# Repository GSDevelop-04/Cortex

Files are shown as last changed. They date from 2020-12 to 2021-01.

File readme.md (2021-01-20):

<br/>
<p align="center">
   <a href="https://github.com/GSDevelop-04/Cortex">
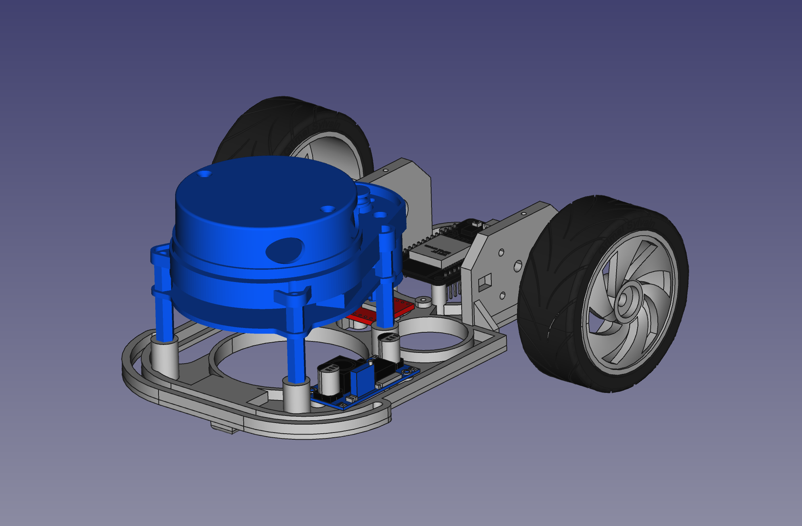
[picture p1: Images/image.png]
    
   </a>
   <br/>
   Plateforme de découverte et d'étude de L'Intelligence Artificielle<br/>
   Véhicule autonome 
</p>

##    1) Introduction

Cortex est un véhicule d'étude de l'Intelligence Artificielle avec réseaux de neurones.
cliquer pour voir la vidéo sur youtube:
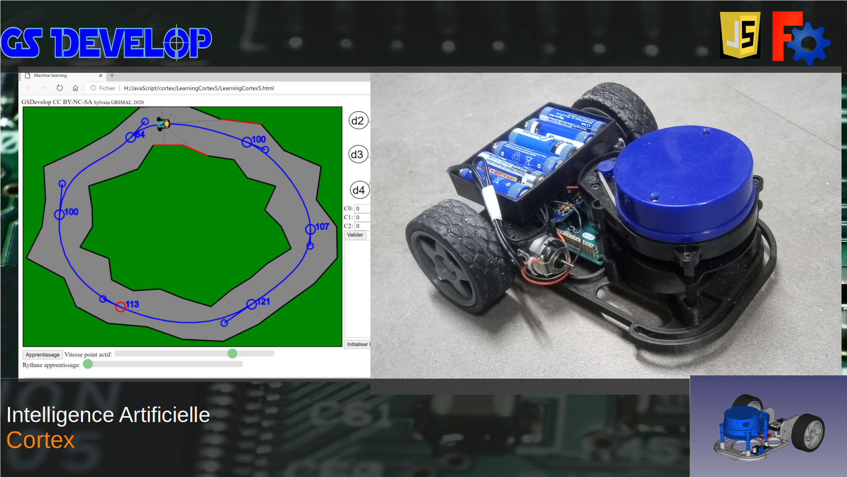
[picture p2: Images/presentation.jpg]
Vidéo (https://youtu.be/U6bnyhtQa3g)


Cette plateforme permet de découvrir les alghorithmes génétiques ainsi que l'apprentissage supervisé.

**Nouveau:  Version 0.2 utilisation d'un piste générée aléatoirement ou un circuit routier**
 
<p align="center">
 <a href="https://github.com/GSDevelop-04/RaceMini">
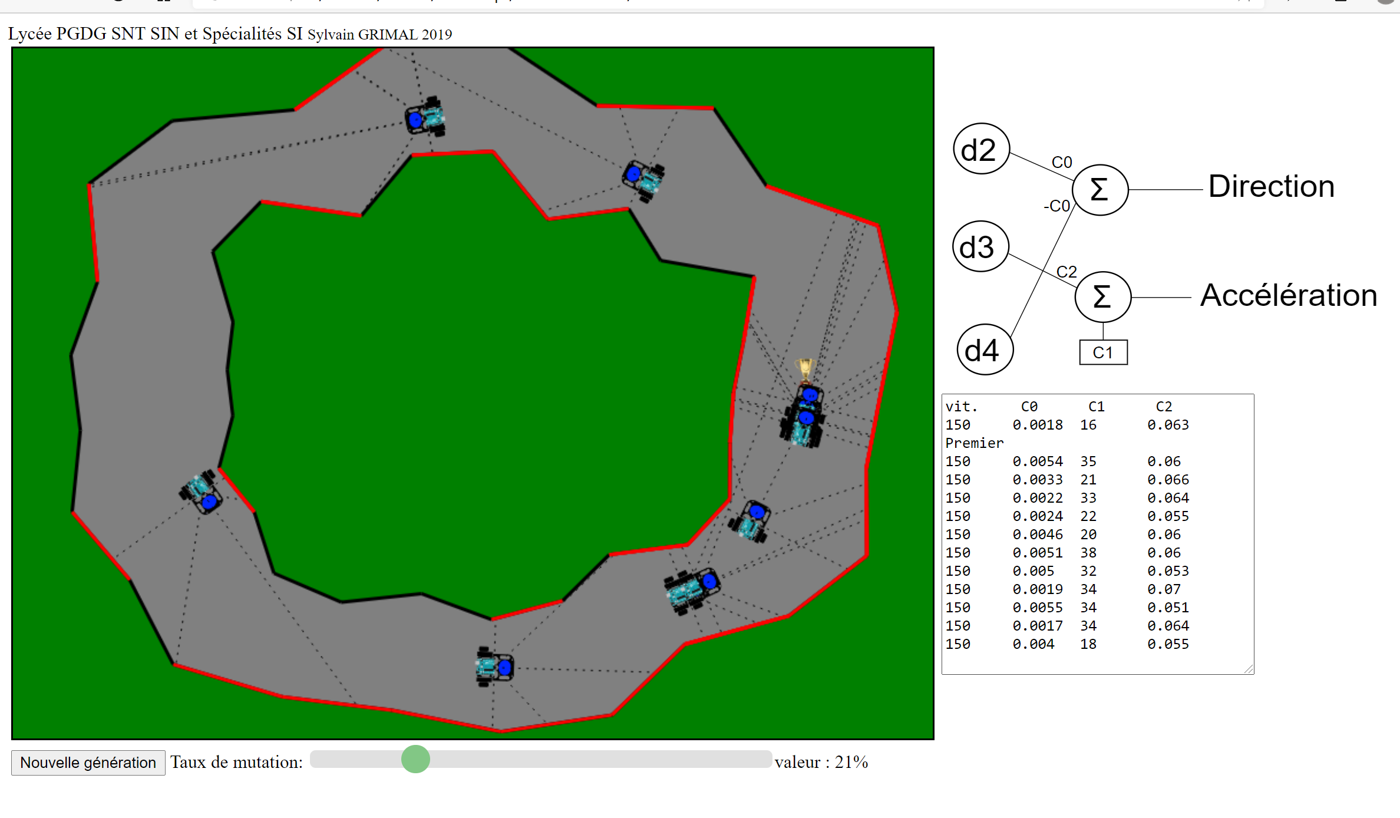
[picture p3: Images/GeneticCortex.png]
    
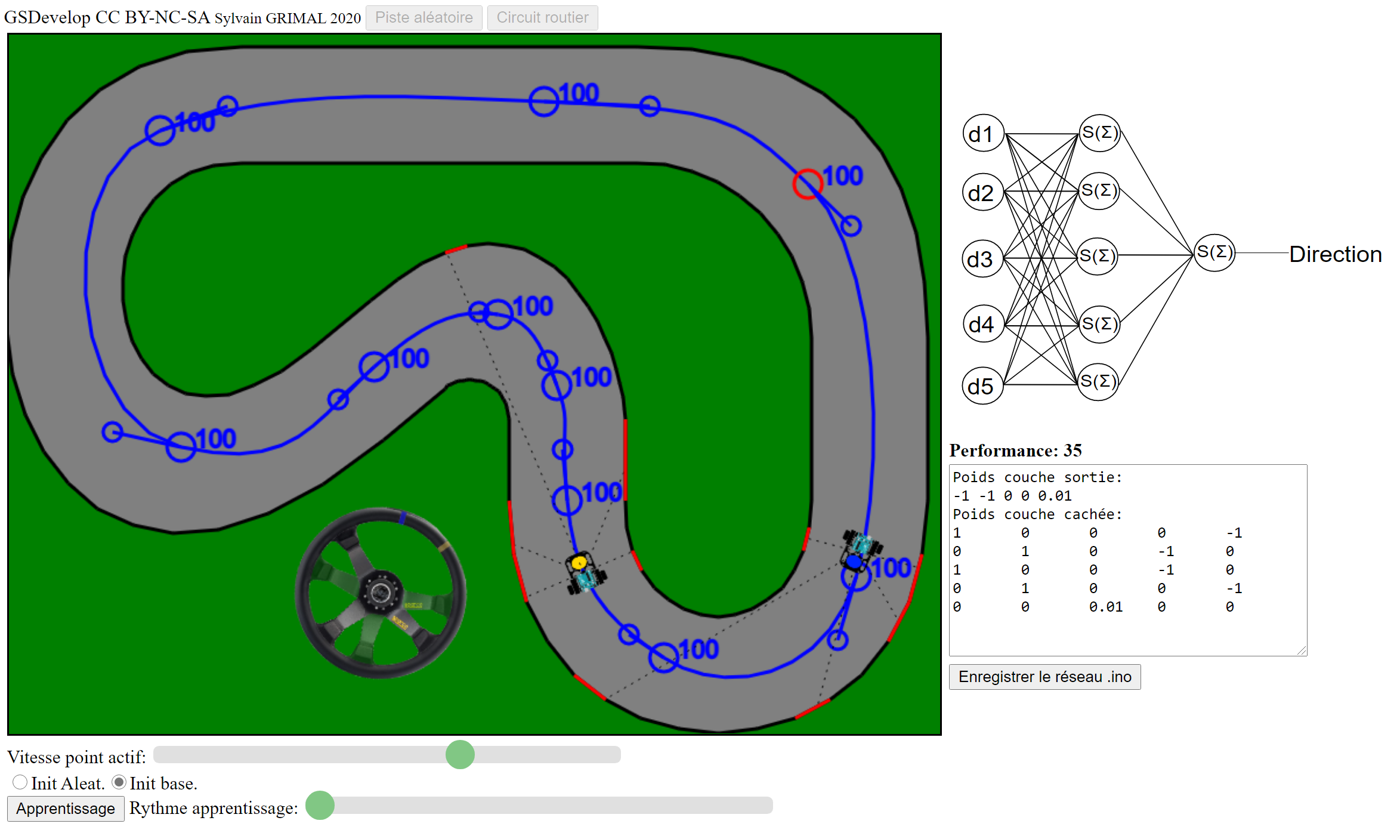
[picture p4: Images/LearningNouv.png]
    
 </a>
</p>

Il comprend des 3 programmes, en javascript, de simulation permettant l'entrainement d'un reseau de neurones ainsi qu'un petit véhicule réel d'experimentation.
Le véhicule perçoit son environement grâce à un lidar "YDlidar X4". L'utilisation d'un "X2" est en cours de developpement.

Nb: le lidar X4 a une vitesse de transmission série de 128 000 bps, non standard, elle le rend incompatible avec une carte Uno (cf. diviseur de fréquence) le "X2" a une vitesse de 115 200 bps mais le flux continu des données risque de saturer un µp à 8 Mhz. La taille du tampon de données doit, d'ailleurs, être augmentée sur une Due: C:\Users\xxxxxxx\AppData\Local\Arduino15\packages\arduino\hardware\sam\1.6.12\cores\arduino\RingBuffer.h #define SERIAL_BUFFER_SIZE 64 par defaut 512 pour éviter les erreurs.

<p align="center">
 <a href="https://github.com/GSDevelop-04/RaceMini">
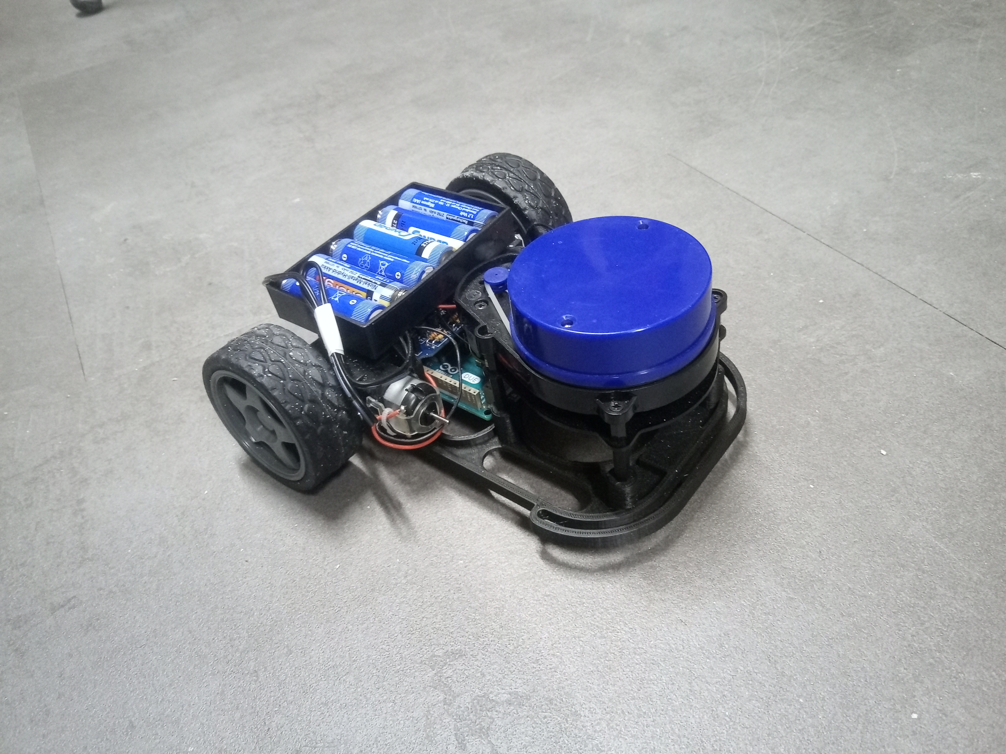
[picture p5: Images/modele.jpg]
    
 </a>
</p>

La version la plus simple comprend 5 neurones: 3 de présentation et 2 de sortie.

Il existe aussi une version à 12 neurones: 5 de présentation, 5 d'une couche intermédiaire et 2 de sortie.
 
La couche de présentation contient les 5 distances du véhicule au bord de la route dans 5 directions (-90° -45° 0° 45° 90°)

**GeneticCortex5:** Version pour découvrir les algorithmes génétiques avec 5 neurones ( seules les distance à -45° 0° et 45° sont utilisées ) et seulement 3 poids synaptiques (dont 1 biais).  Les gènes sont directement les poids synaptiques. La premiere génération utilise des poids générés aléatoirement.<br/>
Seul le véhicule de tête voiture peut se reproduire, A chaque nouvelle génération les poids prennent une valeur entre ceux du parent et une valeur aléatoire en fonction d'un taux de mutation ( taux de 0: tous les enfants ont les mêmes caractéristiques que le parent, taux de 1: chaque génération ne depend pas du parent )<br/>
Avec seulement trois gènes l'évolution est très rapide.

**Attention**, il est important de comprendre que vue la structure utilisée (pas de vision globale de la route, pas de neurone recursif) il est illusoire d'obtenir de l'anticipation avant le virage (déport à droite pour tourner à gauche, passage à la corde puis élargissement de la trajectoire etc.) imaginez vous conduire avec seulement comme indication la distance du bord de route à 45° droite, en face et à 45° gauche !

**LearningCortex5:** Version pour découvrir l'apprentissage supervisé, on retrouve la configuration neuronale de la version génétique.<br/>
Il est necessaire de definir la trajectoire à suivre à la souris: On peut modifier les points de passages, les tangeantes et aussi la vitesse. Entre les points de passage la vitesse varie linéairement.<br/>
Le véhicule professeur suit la trajectoire, il est possible de récupérer les différents echantillons de l'apprentissage dans un fichier csv qui comprend les trois informations de distance et les valeurs cibles du professeur (direction et vitesse).<br/>
Les calculs des coefficients peuvent être alors fait par regression lineaire dans un tableur: il faut trier les valeurs non significatives (quand d4-d2<100) puis calculer les valeurs par régression lineaire (attention pour la direction la droite doit passer par zero et l'option régression linéaire ne le fait pas, il faut donc entrer les formules).<br/>
Le calcul peut aussi être automatique (on utilise, dans le programme javaScript, pour la direction la moyenne entre la regression horizontale et verticale, on pourrait aussi utiliser une régression orthogonale mais le calcul est un peu plus complexe sans apporter d'avantage significatif )

**LearnigCortex12:** Version à 12 neurones et 42 poids synaptiques (avec les biais), elle est destinée à la découverte de l'apprentissage supervisé avec rétropropagation du gradient d'erreur. La fonction d'activation est une sigmoïde (une version avec fonction ReLu est à l'étude).<br/>
Une premiere version ne comprend que la direction (11 neurones: 1 seul neurone de sortie et 36 poids synaptiques) et permet d'appréhender les calculs de rétropropagation du gradient d'erreur sur la couche de sortie et la couche cachée.<br/>
La version 12 neurones est en cours de developpement.

**Maquette:** Le modèle est entierement imprimable en 3D. Si vous utilisez une Arduino Due il faut couper les fixations de ESP 32 après l'impression. Les coefficients obtenus sur les simulations sont à copier dans le programme Arduino.

**Dans le dépot Cortex vous trouverez :**

* les fichiers CAO, STL pour imprimantes 3D
* Les sources Html et javascript pour l'entrainement
* Le source ESP32 (en cours) ou Arduino Due pour IDE Arduino

L'ensemble est sous licence **CC BY-NC-SA**

**Les éléments suivants sont nécessaires:**

* YDlidar X4 (essai en cours pour passer à un X2, moins cher)
* Arduino Due ou ESP32 ( Il existe de nombreux modules, les fixations sont prévues pour un ESP32 DEVKIT V1: 30 broches)
* Carte double variateur type TB6612 ou DRV8833 ou shield moteur pour Arduino Due
* Module d'alimentation découpage type lm2596
* 2 x Moteurs reductés, roues
* Support de batterie
* Visserie

##    2) Câblage

Le câblage peut être réalisé en fils volants ou avec un circuit imprimé (document KiCad)

<p align="center">
 <a href="https://github.com/GSDevelop-04/Cortex">
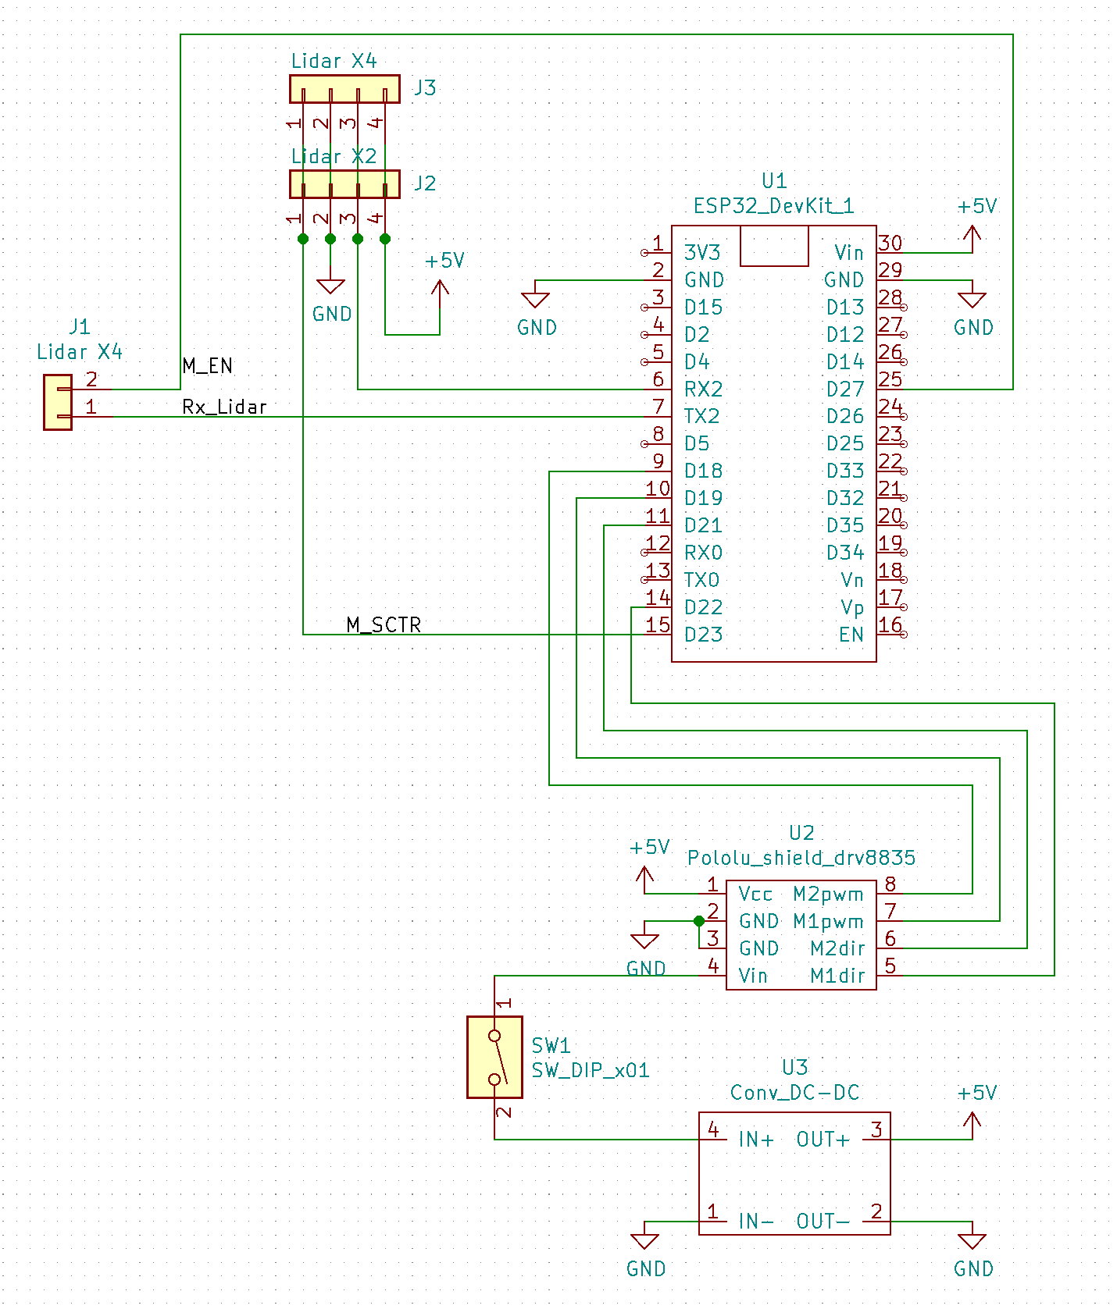
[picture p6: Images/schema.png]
    
 </a>
</p>

**Liasons Arduino Due ou ESP32 Lidar:**  
* Série: Due RX1 / ESP32 RX2           <-> Tx Lidar X4 Tx X2
* Série: Due TX1 / ESP32 TX2           <-> Rx Lidar X4 Nc X2
* Vitesse Moteur Due D7 / ESP32 GPIO 27<-> M_SCTR Lidar X4 M_SCTR X2
* Enable Due D3 / ESP32 GPIO 23        <-> M_EN Lidar X4 Nc X2

**Liaisons Arduino Due ou ESP32 Variateur:**  
* Due D5 /  ESP32 GPIO 19 <-> APWM  // AIN2 DRV8833
* Due D4 /  ESP32 GPIO 22 <-> AIN1  // Marche avant: 0 Marche arrière: 1

* Due D9 /  ESP32 GPIO 21 <-> BPWM  // BIN2 DRV8833 
* Due D12 / ESP32 GPIO 18 <-> BIN1  // Marche avant: 0 Marche arrière: 1

* +3.3 V                  <-> Vcc selon carte
* Vbat                    <-> VM				

**Et les alimentations 5 V:** Le 5v est fourni par un mini-module regulateur 5V à découpage (le lidar consomme trop pour le regulateur Arduino) 

##   3) Vidéos

à faire
* [Présentation: https://youtu.be/U6bnyhtQa3g](https://youtu.be/U6bnyhtQa3g)
* [Algorithme génétique: https://youtu.be/](https://)
* [Apprentissage supervisé: https://youtu.be/](https://youtu.be/)
* [Modélisation caméra sténopé: https://youtu.be/](https://youtu.be/)

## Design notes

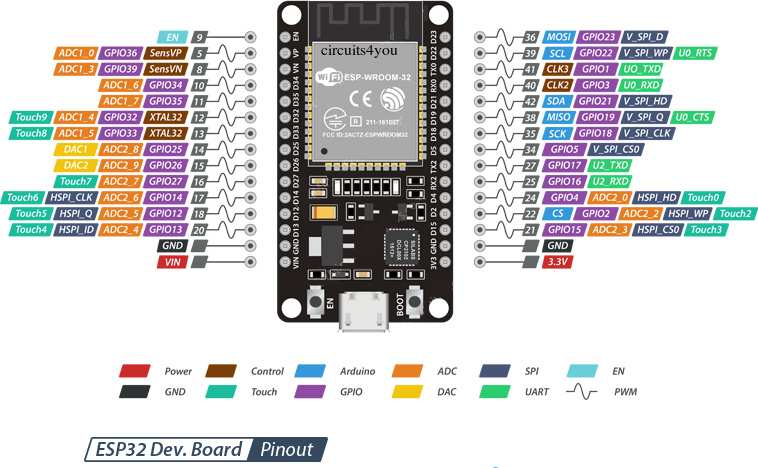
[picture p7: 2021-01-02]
Images/ESP32-Pinout.jpg

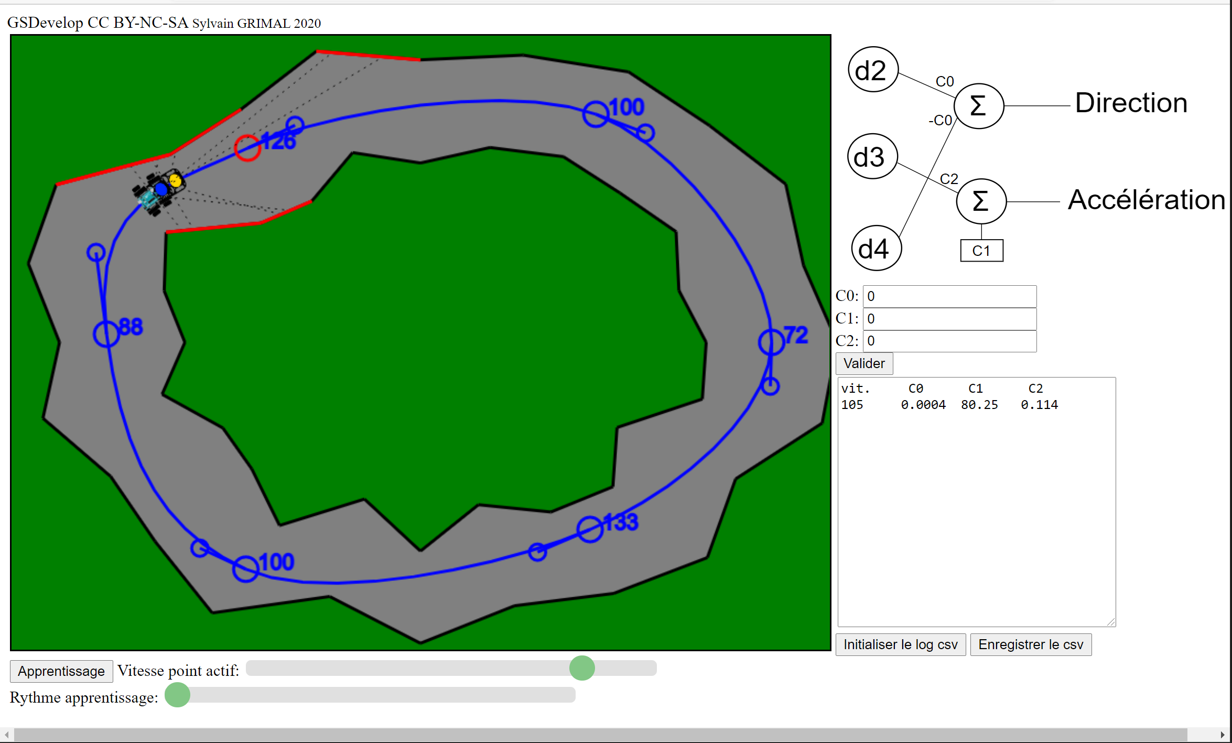
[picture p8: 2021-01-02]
Images/LearningCortex.png

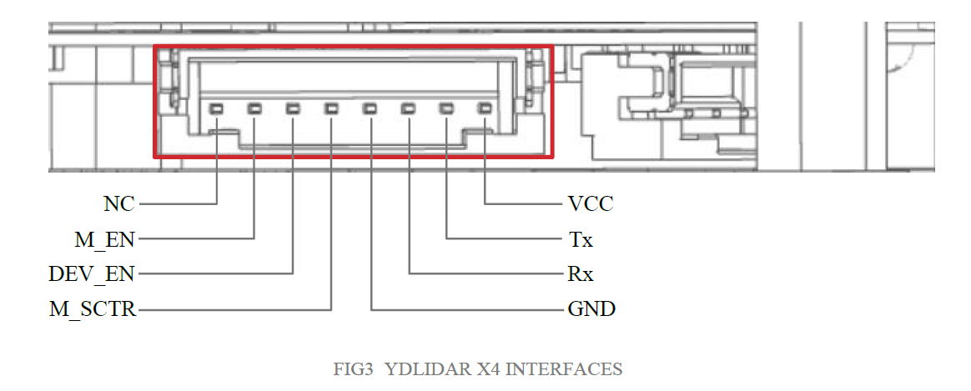
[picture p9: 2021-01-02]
Images/connection X4.png

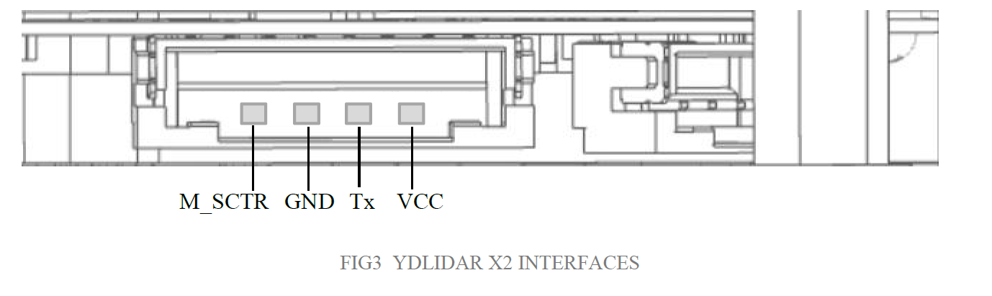
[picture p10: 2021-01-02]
Images/connection X2.png

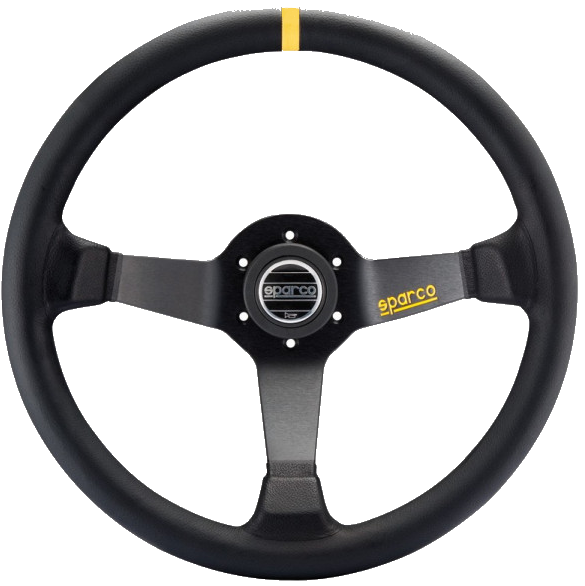
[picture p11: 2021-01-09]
JavaScript/LearningCortex5/volantProf.png

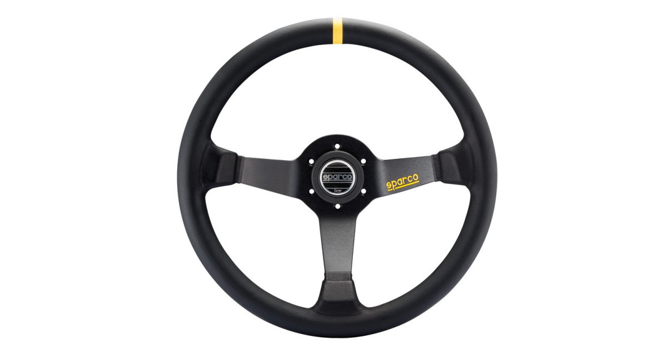
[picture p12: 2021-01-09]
JavaScript/LearningCortex11/volant.jpg

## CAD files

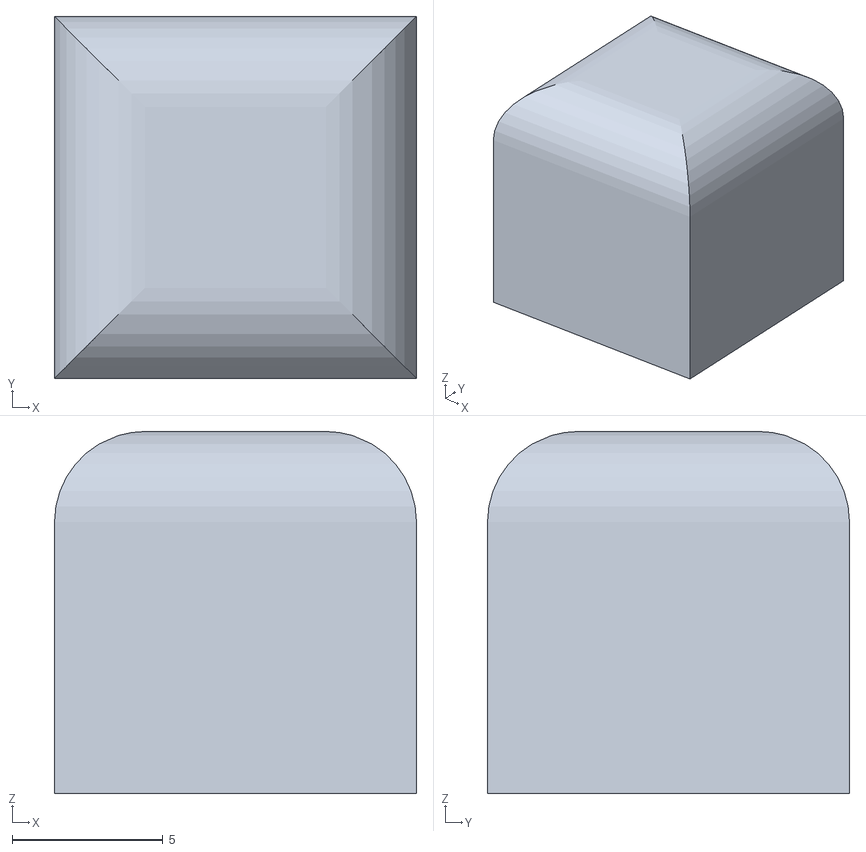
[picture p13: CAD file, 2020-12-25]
CAO/patin.stl
12.0 x 12.0 x 12.0

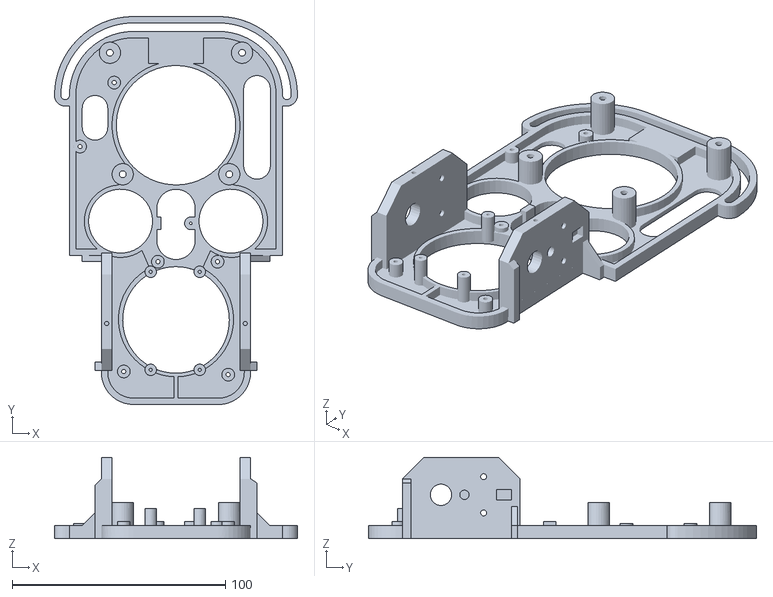
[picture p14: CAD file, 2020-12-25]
CAO/chassis.stl
114.0 x 182.0 x 38.0

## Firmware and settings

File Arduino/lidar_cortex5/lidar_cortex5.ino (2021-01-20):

#include "commandes.h"

// choisir votre carte en mettant en commentaire l'autre
//#define Due
#define ESP32

// Choisir le type de variateur utilisé en mettant en commentaire l'autre
#define VARIADIRPWM  //  Dir PINA1 et PWM PINA2 (shield arduino)
//#define VARIAA1A2    // avant PINA1=0 PINA2=PWM et arriere PINA1=PWM et PINA2=0 (DRV8833 fast decay SLEEP à 1 / TB6612 compatible avec PWM et STBY à 1) 

#if defined(Due)
#define PINA1 4
#define PINA2 5
#define PINB1 12
#define PINB2 9
#define YDLIDAR_MOTOR_SCTP 3 // The PWM pin for control the speed of YDLIDAR's motor. 
#define YDLIDAR_MOTRO_EN   7 // The ENABLE PIN for YDLIDAR's motor      
#define LIDAR Serial1    
#endif
#if defined(ESP32)
#define PINA1 22
#define PINA2 19
#define PINB1 21
#define PINB2 18
#define YDLIDAR_MOTOR_SCTP 23 // The PWM pin for control the speed of YDLIDAR's motor. 
#define YDLIDAR_MOTRO_EN   27 // The ENABLE PIN for YDLIDAR's motor          
#define LIDAR Serial2
#endif

char car;
char octet;
String ordre;
byte trame[256];
float portion[16];
float angleDebut,
      angleFin;
int n,nb;
unsigned int mot;
byte donnees;
byte mode;


bool lid_pause=false;

#define DEBUT 0
#define START 1
#define ENTETE 2
#define DONNEES 3
#define BUG 4
#define BUGSUITE 5
#define RECOMMENCE 6



void setup() {
  // put your setup code here, to run once:
  // init moteurs


#if defined(Due)   
      analogWrite(PINA2,0));
      analogWrite(PINB2,0);
#endif
#if defined(ESP32)
   ledcSetup(0, 10000, 8);   ledcSetup(1, 10000, 8);
   ledcSetup(2, 10000, 8);   ledcSetup(3, 10000, 8);
   ledcAttachPin(PINA1, 0);
   ledcAttachPin(PINA2, 1);
   ledcAttachPin(PINB1, 2);
   ledcAttachPin(PINB2, 3);   
#endif

  //init lidar
  pinMode(YDLIDAR_MOTOR_SCTP, OUTPUT);
  pinMode(YDLIDAR_MOTRO_EN, OUTPUT);  
  digitalWrite(YDLIDAR_MOTRO_EN, LOW);  
  vitesseLidar(70);
  mode=DEBUT;
  n=0;
  nb=0;

  Serial.begin(115200);
  LIDAR.begin(128000);
  
  delay(3000);
  digitalWrite(YDLIDAR_MOTRO_EN, HIGH);
  Serial.println ("C'est parti");
  octet=0xA5;
  LIDAR.write(octet);
  octet=0x40;
  LIDAR.write(octet);
  delay(2000);
  LIDAR.write(scan,2);
  mode=START;
  n=0;
  nb=7;
}

void loop() {

  lidar();

  if (Serial.available()>0) {
    car=Serial.read();
    if (car==13) {
      gestionCommandes(ordre);
      ordre="";
    }
    else if (car>=32) ordre+=car;
  }
}

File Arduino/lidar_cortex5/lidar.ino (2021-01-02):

void lidar(){
  if (LIDAR.available()>0) {
      donnees=LIDAR.read();
      trame[n]=donnees;
      n++;
      if (LIDAR.available()>200){
         LIDAR.write(stop,2);
         lid_pause=true;
      }
      // normalement inutile
      if (((nb==0)||(nb>80))&&(mode!=DEBUT)) {
         //Serial.println("??? attente de resynchronisation !");
         mode=BUG;
         n=0;
         nb=1;
      }
      // recue tous les caracteres attendus
      if (n==nb){
         switch(mode) {
            case START:
               //Serial.println();
               //Serial.print("Debut ");
               //affiche(7);
               mode=ENTETE;
               n=0;
               nb=10;
               break;
            case ENTETE:
               //Serial.println();
               //Serial.print("Entête: ");
               //affiche(10);
               mot = trame[4]>>1;
               mot+= trame[5]<<7;
               angleDebut=(float)mot/64;
               mot = trame[6]>>1;
               mot+= trame[7]<<7;
               angleFin=(float)mot/64;
               if (angleFin<angleDebut) angleFin+=360;
               //Serial.print("Angle début: ");Serial.print(angleDebut);Serial.print(" ");
               //Serial.print("Angle fin: ");Serial.println(angleFin);
                                 
               if ((trame[0]==0xAA)&(trame[1]==0x55)&(trame[2]==0)) {
                  nb=trame[3]*2;
                  //Serial.print("Attente de: "); Serial.print(nb); Serial.println(" caractere(s)");              
                  mode=DONNEES;           
                  n=0;
               } else 
                  if ((trame[0]==0xAA)&(trame[1]==0x55)&(trame[2]==1)) {
                     nb=trame[3]*2;
                     //Serial.print("Trame Zero: "); Serial.print(nb); Serial.println(" caractere(s)");              
                     mode=DONNEES;           
                     n=0;
                  } else {
                     // bug
                     //Serial1.write(stop,2);
                     //Serial1.write(scan,2);
                     //Serial.println("attente de resynchronisation !");
                     mode=BUG;
                     n=0;
                     nb=1;
                  }
               
               break;
            case DONNEES:
                  //Serial.println();
                  //Serial.print("donnees: ");
                  affiche(nb);
                  mode=ENTETE;
                  n=0;
                  nb=10;
                break;

            case BUG:
                if (trame[0]==0xAA) {                  
                  mode=BUGSUITE;
                  n=0;
                  nb=1;
                } else {
                  n=0;
                  nb=1;
                }
                break;
            
            case BUGSUITE:
                if (trame[0]==0x55) {                  
                  mode=RECOMMENCE;
                  n=0;
                  nb=8;
                }
                break;

            
            case RECOMMENCE: // ne devrait pas arriver avec gestion buffer
              //Serial.println();
              //Serial.print("Resynchronisé: ");
              //affiche(8);                  
              if (trame[0]==0) {
                  nb=trame[1]*2;
                  //Serial.print("Attente de: "); Serial.print(nb); Serial.println(" caractere(s)");              
                  mode=DONNEES;           
                  n=0;
               } else 
                  if (trame[0]==1) {
                     nb=trame[1]*2;
                     //Serial.print("Trame Zero: "); Serial.print(nb); Serial.println(" caractere(s)");              
                     mode=DONNEES;           
                     n=0;
                  } else {
                     // c'etait pas bon !
                     //Serial1.write(stop,2);
                     //Serial1.write(scan,2);
                     //Serial.println("attente de resynchronisation !");
                     mode=BUG;
                     n=0;
                     nb=1;
                  }
                break;

                
         } 
      }
      if (n>255) {Serial.println("POUF!!!!");
         mode=BUG;
         n=0;
         nb=1;
      }
         
  } else {
      // Plus de caractere dans le buffer
      if (lid_pause&&(mode!=DEBUT)) {
         //Serial.println("Redemande Scan");       
         LIDAR.write(scan,2);
         mode=START;
         n=0;
         nb=7;
         lid_pause=false;
      }
  }
}
void affiche(int longueur) {
   float distance;
   float angle;
   static int secteur=16;
   if (longueur>2) {
      for (int n=0; n<(longueur>>1);n++){
             mot=trame[n<<1];
             mot+=trame[(n<<1)+1]<<8;
   
             distance=(float)mot/40;
             angle=angleDebut+(angleFin-angleDebut)*n/((longueur>>1)-1);
             if (angle>=360) angle-=360;
             // un tour ?
             int nvSecteur=trunc((angle+11.25)*16/360);
             if (nvSecteur==16) nvSecteur=0;
             //Serial.print(longueur);Serial.print("\t");
             //Serial.print(nvSecteur);Serial.print("\t");Serial.println(secteur);          
             if ((nvSecteur<secteur)){              
               conduite();
               for (int i=0;i<16;i++)portion[i]=9999;
             }
             secteur=trunc((angle+11.25)*16/360);
             if (secteur==16) secteur=0;
             if ((distance<portion[secteur])&& (distance>1)) portion[secteur]=distance;          
   
      }
   }
   //Serial.println();
}

void vitesseLidar(int pourCent){
#if defined(Due)   
  analogWrite(YDLIDAR_MOTOR_SCTP, 2.56*pourCent);
#endif
#if defined(ESP32)
  ledcWrite(YDLIDAR_MOTOR_SCTP, 10.23*pourCent);
#endif
}

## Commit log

2020-12-25 premier commit
    [chassis.stl, patin.stl]
2021-01-02 Modif ESP32
2021-01-03 Maj ESP32/DRV8833
2021-01-09 Ver 11 Neurones
    [mesure.csv]
